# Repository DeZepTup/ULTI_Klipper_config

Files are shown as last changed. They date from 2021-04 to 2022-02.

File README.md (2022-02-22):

## 0. Репозиторий
Данная конфигурация может не подойти к любому ULTI, однако имеет структурированый вид, а потому удобна в качестве темплейта.  
Eсть предложения? Пишите! Тусовка на [отдельном канале в Telegram](https://t.me/ulti_klipper).
- ./macros - склад макросов, подгружается вся директория. Положить на RPi рядом с конфигом.  
### Если у вас Rocker Feeder:
- printer-rocker_feeder-classic.cfg - Классическая конфигурация, оригинальный Rocker Feeder.
- printer-rocker_feeder-performance.cfg - Версия без интерполейта и без снижения тока на hold (согласно последним данным, может влиять на точность), оригинальный Rocker Feeder. Проверьте, что не перегреваются моторы.
### Если у вас BMG:
- printer-BMG-interpolate.cfg - Конфигурация с интерполейтом, но без снижения тока на hold, BMG от Triangle.
- printer-BMG-performance.cfg - Версия без интерполейта и без снижения тока на hold, BMG от Triangle.
### Если у вас BMG-Mini:
- Ждите, когда моя ленивая жопа его уже поставит.
### Конфиги PrusaSlicer:
- PrusaSlicer_ULTI_Klipper.ini - стабильный, проверенный конфиг.
- PrusaSlicer_ULTI_Klipper-fast.ini - чуть более быстрая версия, разницы по качеству не заметил.

## 1. Установка FLUIDD
- Скачать [образ](https://github.com/cadriel/FluiddPI) и залить его на SD при помощи [balenaEtcher](https://www.balena.io/etcher/)
- Настроить WiFi в **fluiddpi-wpa-supplicant.txt**
- Воткнуть SD карточку в RPi, включить, после загрузки - посмотреть IP подключенного устройства в админке роутера и подключиться по [ssh](https://www.putty.org)  
<span style="color:red">**Login: pi Password: raspberry**</span>
- Обновиться  

```sudo apt-get update ```   
```sudo apt-get upgrade  ```  
```sudo raspi-config [>Update]  ```  
- Настроить RPi через raspi-config (Hostname, Password, Timezone, etc)  

```sudo echo "pi ALL=(ALL:ALL) NOPASSWD:ALL" >> /etc/sudoers```  

## 2. Установка/обновление Klipper
```cd ~/klipper ```   
```git pull ```  
Даже если используем Fluidd, а не Octo,  
```~/klipper/scripts/install-octopi.sh```    
```ls -lrt /dev/serial/by-id/```    
Должны увидеть, что плата SKR подключена.  
>lrwxrwxrwx 1 root root 13 Jan 17 22:12 usb-marlinfw.org_Marlin_USB_Device_0F017012AF4818C85D18BAFAF50020C3-if00 -> ../../ttyACM0  

```make menuconfig```  

[<span style="color:red">**x**</span>] Enable extra low-level configuration options  
    Micro-controller Architecture (LPC176x (Smoothieboard))  --->  
    Processor model (lpc1768 (100 MHz))  --->  
[<span style="color:red">**x**</span>] Target board uses Smoothieware bootloader  
[<span style="color:red">**x**</span>] Use USB for communication (instead of serial)  
    USB ids  --->  
[ ] Specify a custom step pulse duration  
()  GPIO pins to set at micro-controller startup  

```make clean```  
```make```  
```sudo service klipper stop```  

- Прошивка SKR напрямую потребует [другой бутлоадер для LPC1768](http://smoothieware.org/flashing-the-bootloader), но позволяет не открывать подвал.  

```make flash FLASH_DEVICE=/dev/ttyACM0```  
- Проще прошиться через SD. [Удлинитель](https://habr.com/ru/post/206394/) поможет!  
Закидываем на SD файл **klipper.bin**, переименовав его в **firmware.bin**. Включаем SKR, проверяем и запоминаем свой id.  

```ls -lrt /dev/serial/by-id/```  
>lrwxrwxrwx 1 root root 13 Jan 17 23:20 usb-**Klipper**_lpc1768_1270010FC81848AFFABA185DC32000F5-if00 -> ../../ttyACM0  

```sudo service klipper start```  

## 3. Конфигурирование
- Открываем подходящий под конфигурация конфиг (.cfg), корректируем в нем раздел "# Board" (MCU) - ставим свой /dev/serial/by-id/usb-Klipper_lpc1768_**ID**
- Загружаем конфиг в директорию /home/pi/klipper_config/ с именем printer.cfg  
**Так же загружаем директорию macros**
- Заходим браузером на FLUIDD
- Отправляем в консоль FLUIDD **RESTART**

## 4. Базовая калибровка
Команды отправляются из интерфейса Octoprint/Fluidd в консоль как GCODE.
- Калибруем PID экструдера  
```PID_CALIBRATE HEATER=extruder TARGET=230```
- Калибруем PID стола  
```PID_CALIBRATE HEATER=heater_bed TARGET=110```
- Калибруем [концевики](https://www.klipper3d.org/Endstop_Phase.html)  
```ENDSTOP_PHASE_CALIBRATE ```
- Выравниваем [стол](https://www.klipper3d.org/Manual_Level.html)  
```BED_SCREWS_ADJUST```
- Еще раз проверяем концевики, стол должен останавливаться в Z=0.00  
```ENDSTOP_PHASE_CALIBRATE``` 
- Следующая настройка под вопросом, если используется калибровка через щуп - универсальнее использовать Z_OFFSET.  
Это позволит менять его для различного типа филамента через скрипт запуска, например так - START_PRINT BED_TEMP={first_layer_bed_temperature[0]} EXTRUDER_TEMP={first_layer_temperature[0]} Z_GCODE_OFFSET=**-0.03** 
```Z_ENDSTOP_CALIBRATE```
- Проверяем [Extruder rotation distance](https://www.klipper3d.org/Rotation_Distance.html)
- Печатаем пустотелый кубик для калибровки потока и устанавливаем корректное значение Flow в слайсере, даже если калибровали его до этого в Marlin
- Печатаем температурную башню если неизвестна точная температура

## 5.1 [Pressure Advance](https://www.klipper3d.org/Pressure_Advance.html)
**Прежде чем приступить, убедитесь что температура и поток откалиброваны правильно**  

На мой взгляд калибровка должна происходить примерно с тем же ретрактом, что будет использоваться при печати - это вопреки официальной инструкции, что рекомендует использовать "normal retraction amount", а после калибровки - "small value". Такой подход позволит получить более показательные и приближенные к реальным условиям печати результаты калибровки.  
По шагам:
- Калибровка PA с уменьшенным ретрактом (мои значения - 1.75mm длина и 25mm/s скорость ретракта). Шов Aligned по углу позволит легко найти точную высоту.
По углам определяем оптимальную высоту и по формуле (pressure_advance = стартовое_значение + измерянная_высота_в_мм * инкремент_фактор) высчитываем примерно нужное значение.  

```SET_VELOCITY_LIMIT SQUARE_CORNER_VELOCITY=1 ACCEL=500  ```
```TUNING_TOWER COMMAND=SET_PRESSURE_ADVANCE PARAMETER=ADVANCE START=0 FACTOR=.020 ``` 

У меня оптимальное значение в первоначальном тесте было на высоте 25мм, соответственно 0 + 25 * 0.020 = 0.5  
Устанавливаем полученное значение в прошивке в блоке "# Pressure Advance"  
Если у вас ABS и ULTI стандартной конфигурации, а так же вы используете мой конфиг - скорее всего первоначальную калибровку можно пропустить и приступить сразу к следующему шагу.
- Точная калибровка PA. Настройки аналогичны предудыщему шагу, но шов рекомендую Rear - позволит ориентироваться не только по углам, но и по шву.  
Сразу предупреждаю, что данная калибровка требовательна к зрению, так какесли вы находитесь в оптимальном диапазоне разница будет незначительна. Посветить ярким фонариком под острым углом поможет найти оптимальную высоту.  
Так как оптимальное первоначальное значение было у меня 0.5 (и у вас, скорее всего, тоже рядом), калибровка будет происходить в диапазоне от 0.4 до 0.75  

```SET_VELOCITY_LIMIT SQUARE_CORNER_VELOCITY=1 ACCEL=500 ``` 
```TUNING_TOWER COMMAND=SET_PRESSURE_ADVANCE PARAMETER=ADVANCE START=0.4 FACTOR=.007 ``` 

Оптимальная высота у меня составила 26.77мм, соответственно, pressure_advance = <start> + <measured_height> * <factor> = 0.4 + 26.77 * 0.007

- Калибровка square_corner_velocity через все тот же Tung Tower, используя модель ringing_tower.stl (перед тестом нужно завысить лимит square_corner_velocity в конфиге).  

Я не заметил никаких позитивных изменений в качестве при повышении SCV, ровно как и повышения скорости печати. После 30 появилось эхо. Если вдруг у вас иные результаты - пожалуйста сообщите. Похоже, что значения в **5** вполне достаточно при печати 100mm/s и 3000mm^2/s. Если есть желание, то - 
```TUNING_TOWER COMMAND=SET_VELOCITY_LIMIT PARAMETER=SQUARE_CORNER_VELOCITY START=5 FACTOR=1```

## 5.2 Альтернативная калибровка Pressure Advance
Выполнить печать STL/PA_calibratiob_v*.stl в режиме калибровочной башни. Слайсинг - с обычными, часто используемыми параметрами печати, а печать без изменений SCV и ускорений.
```TUNING_TOWER COMMAND=SET_PRESSURE_ADVANCE PARAMETER=ADVANCE START=0.4 FACTOR=.007 ``` 
Данная модель покажет слишком раннюю или слишком позднюю, либо недостаточную или чрезмерную компенсацию. Стоит обратить внимание не только на углы, но и на окончание периметра в прорези.
Версии различаются по ширине линии. 

# Ура! Первоначальная калибровка завершена, теперь можно печатать кораблики и кубики!

## TODO
- firmware_retraction + fine retraction calibration (tower)
- Not sure about correct retraction/deretraction acceleration - max_extrude_only_accel  
- Fan tower
- Accel tower
- Speed tower
- Написать раздел по https://www.klipper3d.org/Resonance_Compensation.html
- Проверить https://www.klipper3d.org/skew_correction.html
- Max smoothing (from accelerometer log) - автоматизировать подбор скриптом.
- Settings per material (retract, z_offset) - перенесено в слайсер
- Fine-tuning Input Shaping (maybe with PA)

## Useful notes
- https://www.klipper3d.org/Slicers.html

### [**На ZAV/UNI/BOLT**](https://yoomoney.ru/to/4100116514086369?from=auth&contextId=UACB_CAC_803ecb35-61a0-4692-bb9c-d2a35735c8fe)

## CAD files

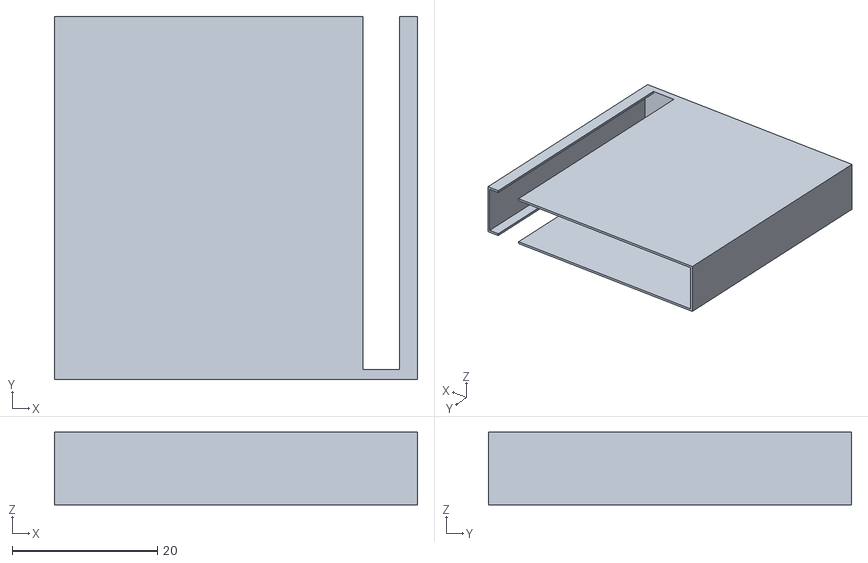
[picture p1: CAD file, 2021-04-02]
STL/PA_calibration_v1.2.stl
50.0 x 50.0 x 10.0

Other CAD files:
STL/PA_calibration_v1.1.stl
STL/PA_calibration_v1.0.stl

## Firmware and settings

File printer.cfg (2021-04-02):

#####################################################################
# Information
#####################################################################
# SKR 1.3
# TMC2208 UART
# Fysetc Mini 12864 LCD Display v2.1 RGB
# Rocker feeder
# 
# CUSTOM:
#     USING RELATIVE EXTRUSION
#     USING 0.050 GAUGE AND OFFSET FOR LEVELING
#     High stealthchop_threshold - not using spreadcycle - https://github.com/KevinOConnor/klipper/issues/1363
#     Slow Z homing and even slower re-homing for perfect leveling
#     Change to rotation_distance - https://github.com/KevinOConnor/klipper/blob/master/docs/Config_Changes.md
# TBD:
#     Firmware retraction
# 
# Useful links:
# Telegram ULTI chat                      https://t.me/ULTI_tigeer
# Telegram AGG channel                    https://t.me/AGG_ULTI_Steel
# Telegram ULTI Klipper channel           https://t.me/ulti_klipper
# Klipper config reference                https://www.klipper3d.org/Config_Reference.html
# List of incompatible slicer features    https://github.com/KevinOConnor/klipper/issues/1869  - Outdated - https://github.com/KevinOConnor/klipper/pull/1997
# S-curve                                 https://github.com/KevinOConnor/klipper/pull/2030
#####################################################################

#####################################################################
# Board
#####################################################################
[mcu]
serial: /dev/serial/by-id/usb-Klipper_lpc1768_1270010FC81848AFFABA185DC32000F5-if00
#baud: 250000

#[mcu]
# https://www.raspberrypi.org/documentation/configuration/uart.md
# https://github.com/KevinOConnor/klipper/issues/2913
# serial: /dev/ttyAMA0

[printer]
kinematics: cartesian
max_velocity: 200
# Need to experiment with max_accel_to_decel - with Resonance Compensation it may do things worse, leading to more resonanse and shaking
# Marlin default is 3000
max_accel: 3000
max_accel_to_decel: 1500
# Probably optimal with fine tuned Resonance Compensation is 5000
#max_accel: 5000
#max_accel_to_decel: 5000
# Use 7000 for resonance calibration
#max_accel: 7000
#max_accel_to_decel: 7000
max_z_velocity: 5
max_z_accel: 100
square_corner_velocity: 5
#####################################################################


#####################################################################
# Resonance - TBD
# https://www.klipper3d.org/Resonance_Compensation.html
#####################################################################
# https://github.com/KevinOConnor/klipper/blob/master/docs/RPi_microcontroller.md
# [mcu rpi]
# serial: /tmp/klipper_host_mcu

# https://github.com/KevinOConnor/klipper/blob/master/docs/Measuring_Resonances.md
# [adxl345]
# cs_pin: rpi:None

# [resonance_tester]
# accel_chip: adxl345
# max_smoothing: 0.1
# probe_points:
#	100,100,20

# RINGING TOWER
# max_accel: 7000
# max_accel_to_decel: 7000
# square_corner_velocity: 5

# [input_shaper]
# shaper_freq_x: 82.81
# shaper_freq_y: 66.25
# shaper_type: mzv

#[scurve]
#acceleration_order: 4
#min_accel: 2500

# [input_shaper]
# shaper_freq_x: 45.2
# shaper_type_x: mzv
# shaper_freq_y: 45.2
# shaper_type_y: mzv
#####################################################################


#####################################################################
# X/Y Stepper Settings
# Microsteps: https://github.com/KevinOConnor/klipper/issues/2999
# rotation_distance = <full_steps_per_rotation> * <microsteps> * <step_distance>
# endstop_phase is not needed for X/Y, but to avoid software endtstop errors may be used
# https://github.com/KevinOConnor/klipper/blob/master/docs/Endstop_Phase.md
#####################################################################
[stepper_x]
microsteps: 64
#interpolate: False
step_pin: P2.2
dir_pin: P2.6
enable_pin: !P2.1
#step_distance: .0125
#rotation_distance = 200 * 16 * 0.0125 = 40
rotation_distance: 40
endstop_pin: P1.29  
position_endstop: 0
position_min: 0
position_max: 200
homing_speed: 40
homing_retract_speed: 10
homing_retract_dist: 10
second_homing_speed: 5

[tmc2208 stepper_x]
#microsteps: 16
interpolate: False
uart_pin: P1.17
run_current: 0.900
hold_current: 0.500
stealthchop_threshold: 5000

[endstop_phase stepper_x]
trigger_phase: 43/64

[stepper_y]
microsteps: 64
#interpolate: False
step_pin: P0.19
dir_pin: !P0.20
enable_pin: !P2.8
#step_distance: .0125
#rotation_distance = 200 * 16 * 0.0125 = 40
rotation_distance: 40
endstop_pin: P1.27  
position_endstop: 0
position_min: 0
position_max: 200
homing_speed: 40
homing_retract_speed: 10
homing_retract_dist: 10
second_homing_speed: 5
 
[tmc2208 stepper_y]
#microsteps: 16
interpolate: False
uart_pin: P1.15
run_current: 0.900
hold_current: 0.500
stealthchop_threshold: 5000

[endstop_phase stepper_y]
trigger_phase: 45/64
#####################################################################


#####################################################################
# Z Stepper Settings
#####################################################################
[stepper_z]
microsteps: 128
#interpolate: False
step_pin: P0.22
dir_pin: P2.11
enable_pin: !P0.21
#step_distance: .000625
#rotation_distance = 200 * 16 * 0.000625 = 2
rotation_distance: 2
endstop_pin: P1.25
position_endstop: 0
position_min: 0
position_max: 270
homing_speed: 5
homing_retract_speed: 2
homing_retract_dist: 2
second_homing_speed: 0.5

[tmc2208 stepper_z]
#microsteps: 16
interpolate: False
uart_pin: P1.10
run_current: 0.650
hold_current: 0.450
stealthchop_threshold: 5000

[endstop_phase stepper_z]
trigger_phase: 34/64
#####################################################################


#####################################################################
# Extruder
# DO     PID_CALIBRATE HEATER=extruder TARGET=230    !
# https://github.com/KevinOConnor/klipper/blob/master/docs/Config_checks.md#calibrate-pid-settings
#####################################################################
[extruder]
microsteps: 32
#interpolate: False
step_pin: P2.13
dir_pin: P0.11
enable_pin: !P2.12
# https://voron.dozuki.com/Guide/Extruder+Calibration+(ESTEPS)/1
#step_distance: 0.0067
#rotation_distance = 200 * 16 * 0.0067 = 21.44
rotation_distance: 21.44
nozzle_diameter: 0.800
filament_diameter: 1.750
heater_pin: P2.7
sensor_pin: P0.24
#   Type of sensor - common thermistors are "EPCOS 100K B57560G104F",
#   "ATC Semitec 104GT-2", "NTC 100K beta 3950", "Honeywell 100K
#   135-104LAG-J01", "NTC 100K MGB18-104F39050L32", "SliceEngineering
#   450", and "TDK NTCG104LH104JT1". See the "Temperature sensors"
#   section for other sensors. This parameter must be provided.
sensor_type: ATC Semitec 104GT-2
pullup_resistor: 4700
min_extrude_temp: 140
min_temp: 10
max_temp: 260
max_extrude_only_accel: 10000
max_extrude_only_velocity: 300
max_extrude_only_distance: 1000
#instantaneous_corner_velocity: 1
#control: watermark # USE FOR START, LATER DO PID_CALIBRATE HEATER=extruder TARGET=230
#max_delta: 0.5 # REMOVE AFTER PID CALIBRATION
# PID without cooling for NTC 100K beta 3950:      pid_Kp=20.627 pid_Ki=1.050 pid_Kd=101.328
# PID with cooling for NTC 100K beta 3950:         pid_Kp=23.688 pid_Ki=1.449 pid_Kd=96.826
# PID without cooling for EPCOS 100K B57560G104F:  pid_kp=24.806 pid_ki=1.344 pid_kd=114.416 | pid_Kp=23.921 pid_Ki=1.276 pid_Kd=112.131
# PID with cooling for EPCOS 100K B57560G104F:     pid_Kp=28.071 pid_Ki=1.642 pid_Kd=120.002
# PID with cooling for EPCOS 100K B57560G104F,
# with heated bed and from cold extruder temp:     pid_Kp=28.081 pid_Ki=1.671 pid_Kd=117.941
# PID without cooling for EPCOS 100K B57560G104F,
# with unheated bed and from room temperature:     pid_Kp=24.156 pid_Ki=1.342 pid_Kd=108.702
# PID_CALIBRATE HEATER=<config_name> TARGET=<temperature> [WRITE_FILE=1]
control: pid
pid_kp: 23.550
pid_ki: 1.236
pid_kd: 112.155

#####################################################################
# Pressure Advance
# https://github.com/KevinOConnor/klipper/blob/master/docs/Pressure_Advance.md
#pressure_advance: 0.333 #0.8 Nozzle
#pressure_advance: 0.585
pressure_advance: 0.5
pressure_advance_smooth_time: 0.040000
#####################################################################
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

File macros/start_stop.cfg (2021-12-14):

#####################################################################
# Start Print and End Print
# Replace the slicer's custom start and end g-code scripts with
# START_PRINT and END_PRINT.
# But not sure if it need to be in config rather than slicer
#####################################################################
[gcode_macro START_PRINT]
default_parameter_BED_TEMP: 110
default_parameter_EXTRUDER_TEMP: 230
default_parameter_Z_GCODE_OFFSET: -0.04
gcode:
    # Reset the G-Code Z offset (adjust Z offset if needed)
    SET_GCODE_OFFSET Z={Z_GCODE_OFFSET}
    # Set relative extrusion
    M83
    # Start bed heating
    M140 S{BED_TEMP}
    # Use absolute coordinates
    G90
    # Home the printer
    G28
    # Move the nozzle near the bed
    G1 Z5 F3000
    # Move the nozzle very close to the bed
    G1 Z0.15 F300
    # Wait for bed to reach temperature
    M190 S{BED_TEMP}
    # Set and wait for nozzle to reach temperature
    M109 S{EXTRUDER_TEMP}
    M117 Printing...

[gcode_macro END_PRINT]
gcode:
    # Turn off bed, extruder, and fan
    M140 S0
    M104 S0
    M106 S0
    # Move nozzle away from print while retracting
    G91
    G1 X-2 Y-2 E-3 F300
    # Raise nozzle by 10mm
    G1 Z10 F3000
    # Absolute positioning
    G90
    # Move bed down
    G0 Z250
    BEEP_CONFIRM
    # Home and deretract, so no empty nozzle
    G28 X0 Y0
    G1 E3 F300
    G90
    # Disable steppers
    M84
    BEEP_ALERT
    M117 Done!
#####################################################################
[gcode_macro LOAD_FILAMENT]
gcode:
    M83
    G1 E600 F1800
    G1 E15 F300
    G1 E15 F150
    # M82
	M117 Load Complete!

[gcode_macro UNLOAD_FILAMENT]
gcode:
    M83
    G1 E10 F300
    G1 E-620 F1800
    # M82
#####################################################################

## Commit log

2021-01-18 Final for today
    [printer.cfg]
2021-01-18 Slow Z re-homing
    [printer.cfg]
2021-01-18 LOAD/UNLOAD, Step adjusteed and well rounded, sensor changed
    [printer.cfg]
2021-01-18 Change from step_distance to rotation_distance
    [printer.cfg]
2021-01-18 Fix microsteps - extruder instead of driver
    [printer.cfg]
2021-01-18 PID fight
    [printer.cfg]
2021-01-19 Fresh config example :)
    [Ruslan.cfg]
2021-01-31 Tiny update
    [printer.cfg]
2021-02-01 timeout + readme
    [printer.cfg]
2021-02-05 Added extruder configuration for 0.8 nozzle
    [printer.cfg]
2021-02-19 Small update.
    0.8 removed
    [printer-basic.cfg]
2021-02-19 All the calibration to the plan
2021-02-20 Guide update
    [printer-basic.cfg]
2021-02-22 Move to Z270 after completion
    [start_stop.cfg]
2021-02-22 Max Z270, cleanup, PA, TG link
    [printer-basic.cfg]
2021-02-22 No need yet
    [printer.cfg]
2021-02-22 Pressure Advance guide release
2021-04-02 Update with experiments
    Z reduced to 250 - Z nut in under table holder
    New miscrostepping experimental setting
    Menu for bed leveling
    [bedScrewMenu.cfg, printer-basic-experimental_v1.cfg, printer-basic-experimental_v2.cfg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]
2021-04-02 PA stress test
    Instruction TBD
    Если кратко - печатать с обычными настройками в режиме калибровочной башни.
    TUNING_TOWER COMMAND=SET_PRESSURE_ADVANCE PARAMETER=ADVANCE START=0.3 FACTOR=.007
    Затем можно проверить lookahead, но стоковое значение подходит хорошо.
    TUNING_TOWER COMMAND=SET_PRESSURE_ADVANCE PARAMETER=SMOOTH_TIME START=0.010000 FACTOR=.002
    [PA_calibration_v1.0.stl, PA_calibration_v1.1.stl, PA_calibration_v1.2.stl]
2021-04-02 Bed PID
    [printer-basic-experimental_v1.cfg, printer-basic-experimental_v2.cfg, printer-basic.cfg]
2021-04-02 control: pid
    [printer-basic-experimental_v1.cfg, printer-basic-experimental_v2.cfg, printer-basic.cfg]
2021-04-03 max_accel_to_decel: 1000
    [printer-basic-experimental_v2.cfg, printer-basic.cfg]
2021-12-14 Update start_stop.cfg
    default_parameter_Z_GCODE_OFFSET: -0.04
    [start_stop.cfg]
2021-12-14 Rework, added BMG
    [printer-BMG.cfg, printer-basic-experimental.cfg, printer-basic.cfg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]
2022-01-14 hold_current removed
    [printer-BMG.cfg]
2022-01-14 stealthchop_threshold: 999999
    [printer-BMG.cfg]
2022-01-14 interpolate: False
    [printer-BMG.cfg]
2022-01-14 Link corrected
    [printer-BMG.cfg]
2022-02-22 Macro update
    thx to Sergey
    [bedScrewMenu.cfg, display_sound.cfg, experimental.cfg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]
